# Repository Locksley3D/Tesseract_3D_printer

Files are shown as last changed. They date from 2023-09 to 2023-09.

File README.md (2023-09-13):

# Tesseract 3D printer

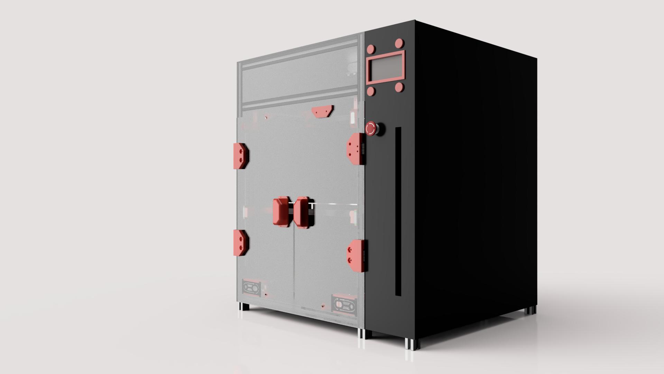
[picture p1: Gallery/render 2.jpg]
Side render of the Tesseract 3D printer


### This repository contains all the design files, scripts, and configs for the Tesseract, A big format tool-changing 3D printer

Some notes for anyone trying to replicate this project. Every STL is sorted in the STL directory and anything that doesn't fit in any categories is in the useful prints section. Also while there is a BOM there might be some small things missing like screws and such, Furthermore if you are using the BOM as a purchasing guide, you should always get more of the small stuff like screws because there are screws for stuff like the electronics mounts that are not in the BOM. If you do decide to build this printer I want to reiterate that this is a project and not a printer that will work right after building. I would be glad to answer any and all questions about thing printer which you can either leave here as an issue or as a comment on the YouTube videos that are linked below 

[Overview on YouTube](https://www.youtube.com/watch?v=-t1q_ze4PNQ)

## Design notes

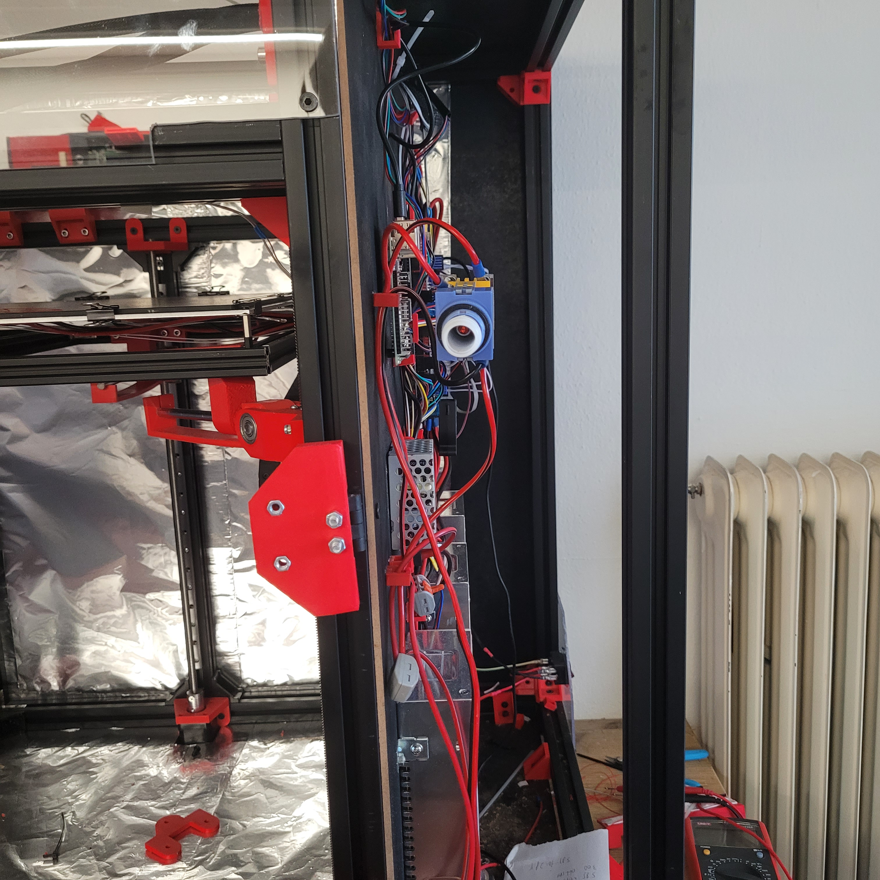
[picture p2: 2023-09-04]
Gallery/Electronics Side.jpg

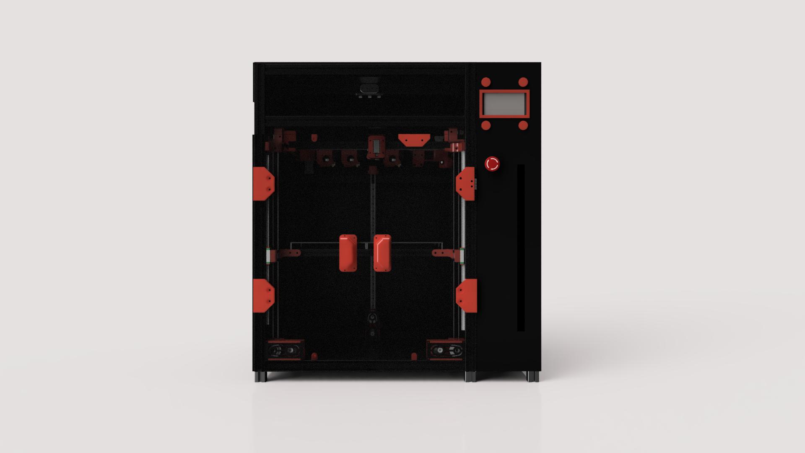
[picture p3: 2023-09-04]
Gallery/render 3.jpg

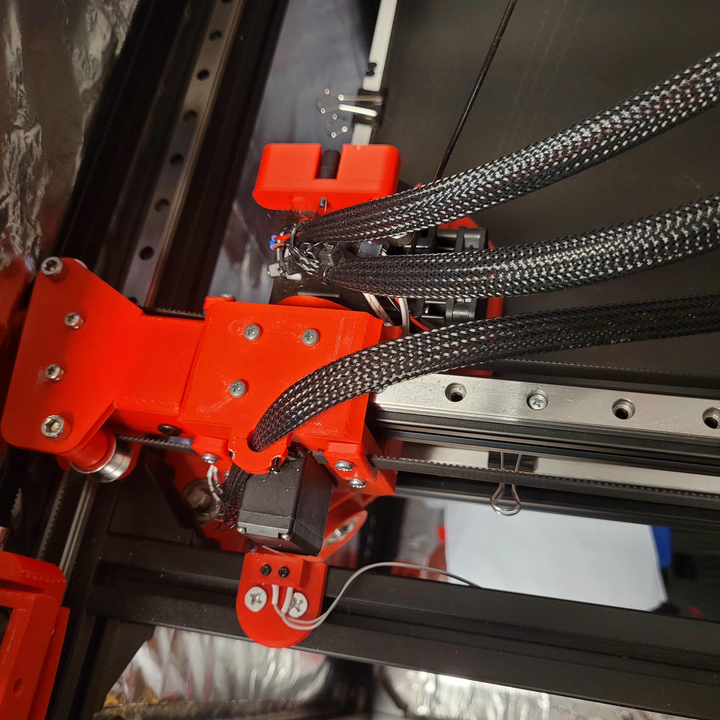
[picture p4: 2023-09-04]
Gallery/Toolhead mounted.jpg

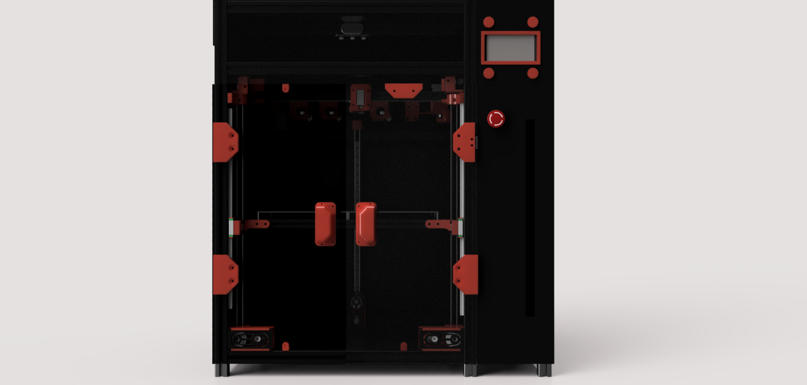
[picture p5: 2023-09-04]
Gallery/render 1.png

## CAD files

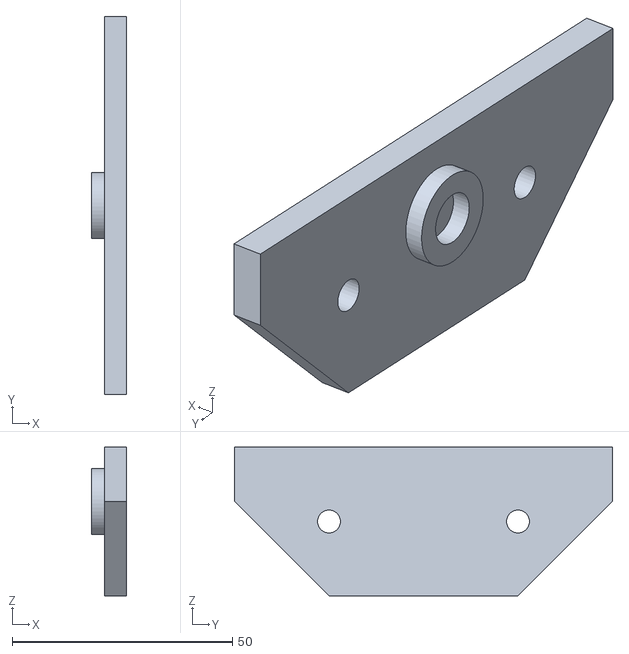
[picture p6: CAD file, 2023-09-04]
STLs/enclosure/door magnet mount.stl
8.00 x 85.9 x 33.8

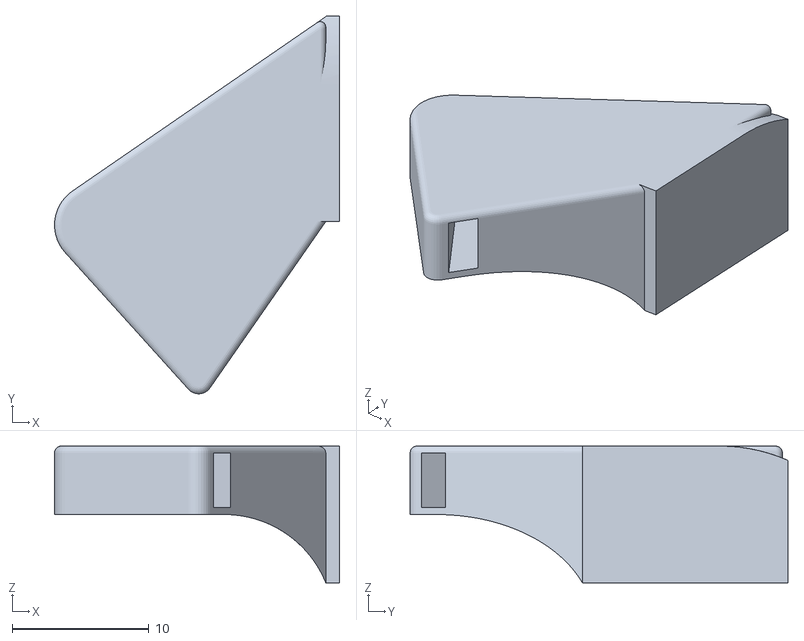
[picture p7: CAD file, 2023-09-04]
STLs/toolhead/toolhead zip tie mount.stl
20.8 x 27.6 x 10.0

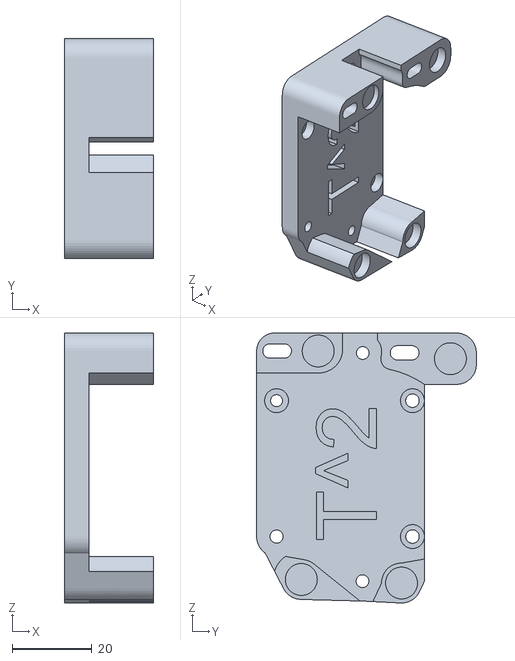
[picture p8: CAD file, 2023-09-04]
STLs/tools/hemera docking plate.stl
22.2 x 55.0 x 67.6

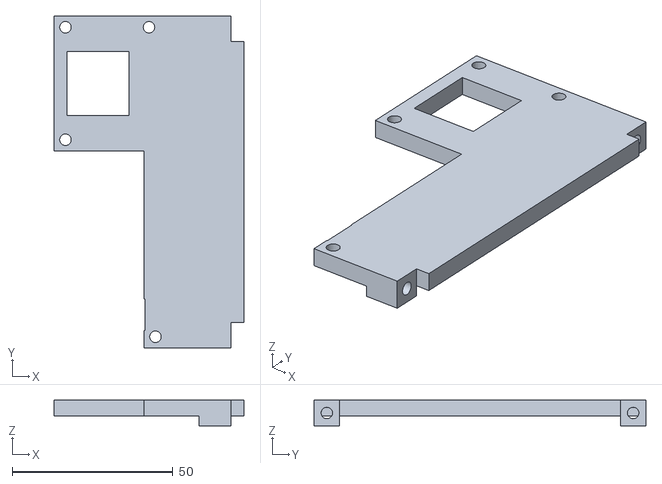
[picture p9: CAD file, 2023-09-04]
STLs/usefull prints/right transmission top plate.stl
59.0 x 103.3 x 8.00

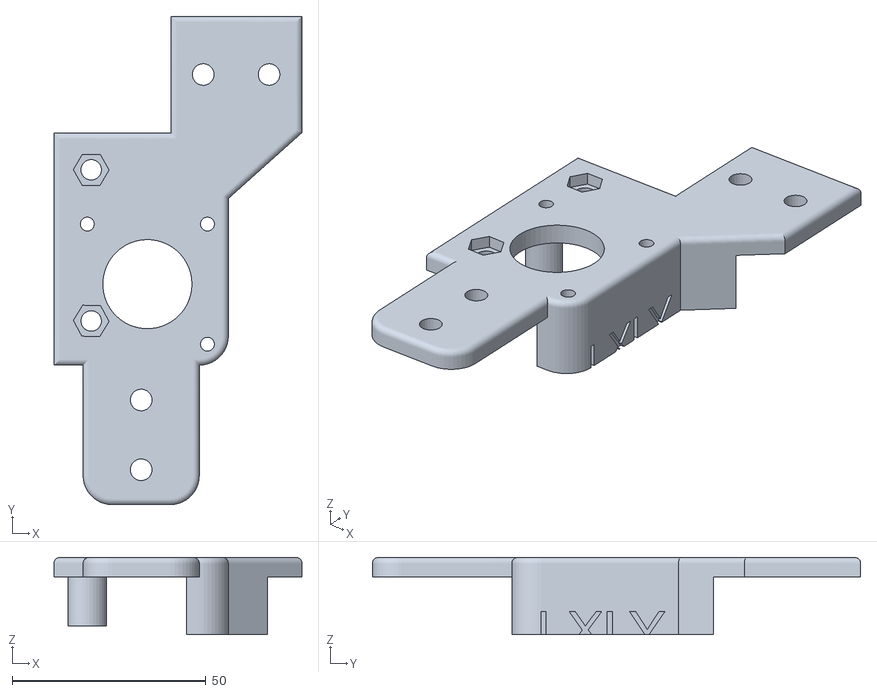
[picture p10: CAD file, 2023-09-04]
STLs/xy axis/right stepper mount to.stl
64.0 x 126.0 x 19.9

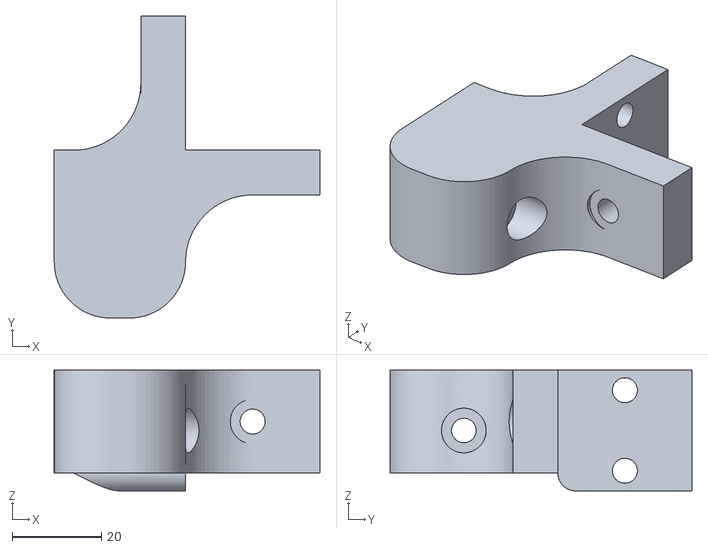
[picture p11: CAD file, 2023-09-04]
STLs/z axis/right belt idler mount.stl
59.3 x 67.5 x 27.0

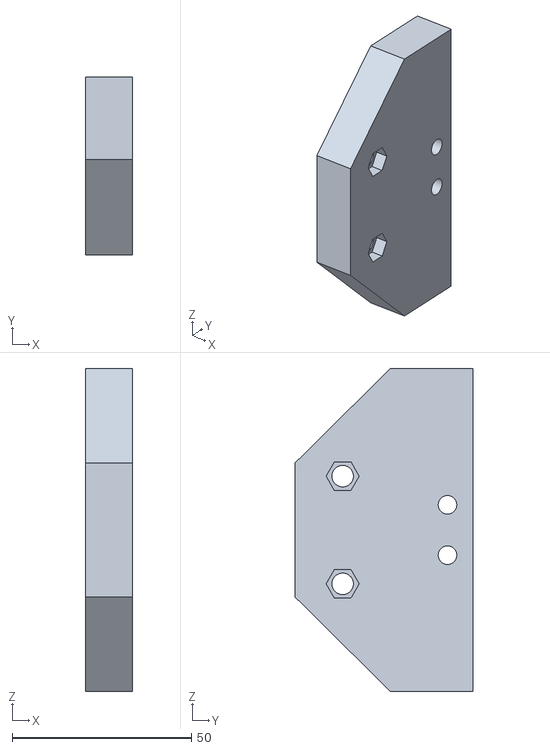
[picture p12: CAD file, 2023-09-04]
STLs/enclosure/right hinge.stl
13.0 x 49.6 x 90.0

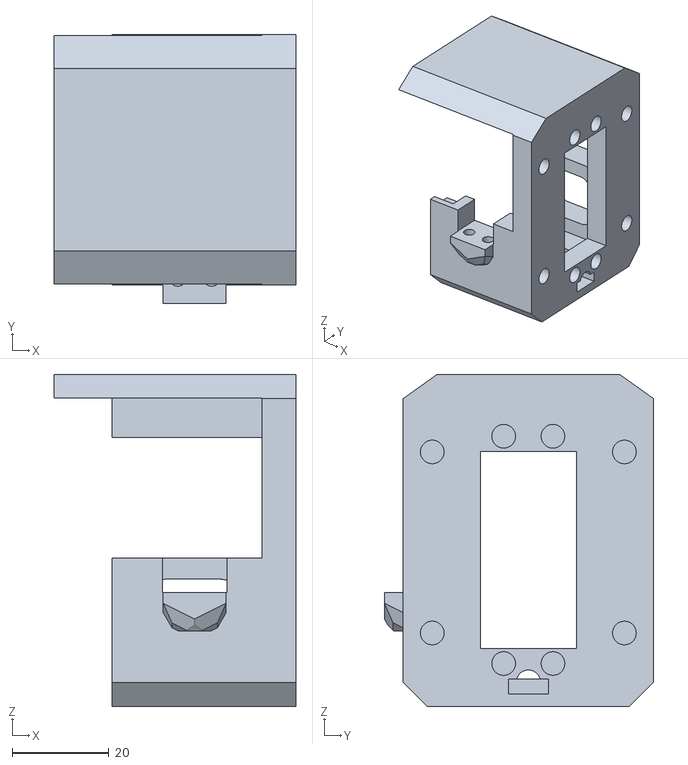
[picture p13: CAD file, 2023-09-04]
STLs/toolhead/toolhead servo mount.stl
49.9 x 55.5 x 68.5

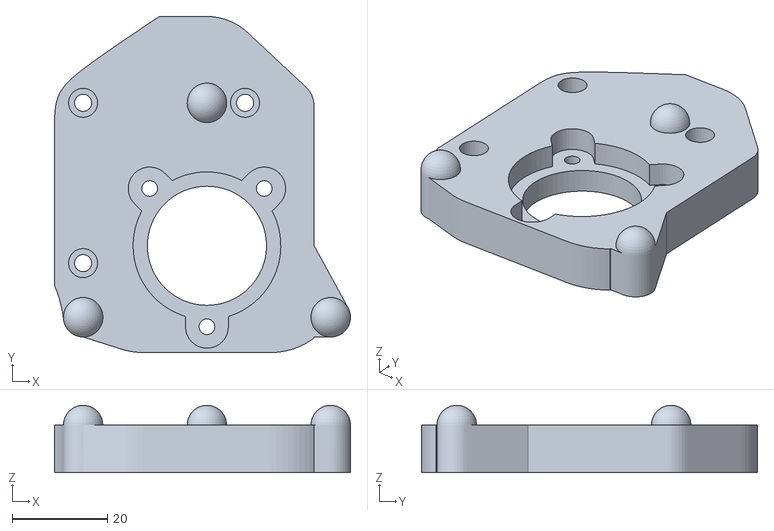
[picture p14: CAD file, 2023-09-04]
STLs/tools/hemera toolplate.stl
62.1 x 70.5 x 14.1

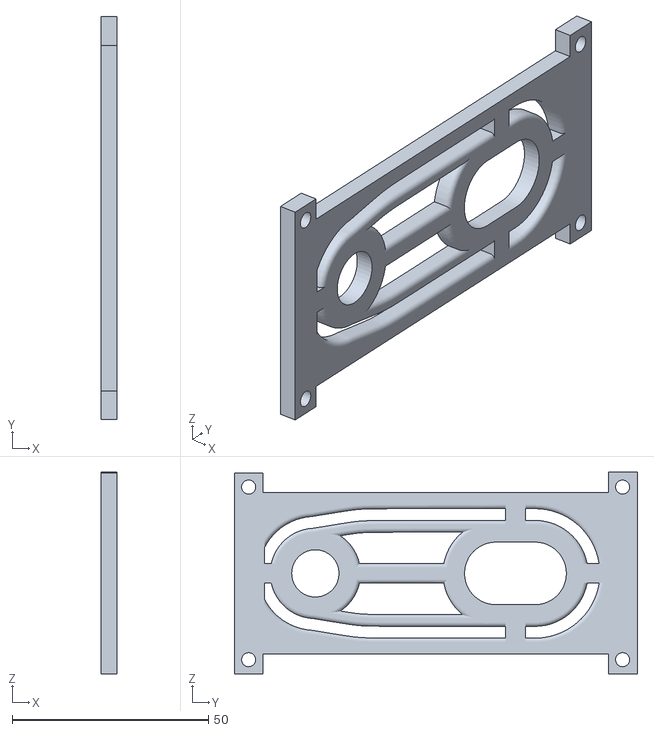
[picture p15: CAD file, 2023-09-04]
STLs/usefull prints/left transmission faceplate.stl
4.00 x 102.7 x 51.4

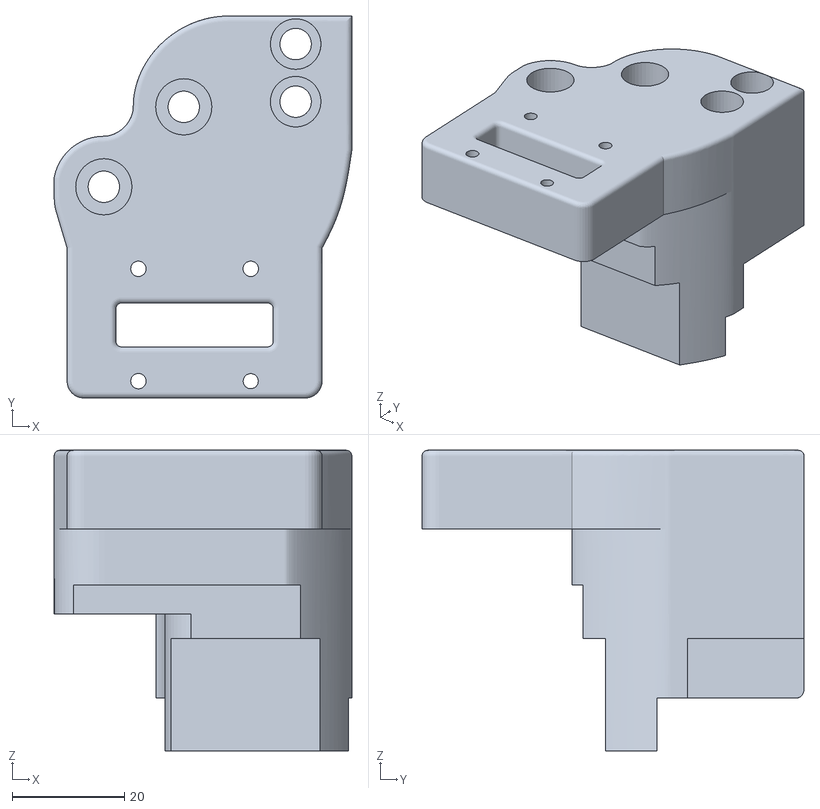
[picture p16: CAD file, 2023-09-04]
STLs/xy axis/left x gantry block.stl
53.0 x 68.0 x 53.5

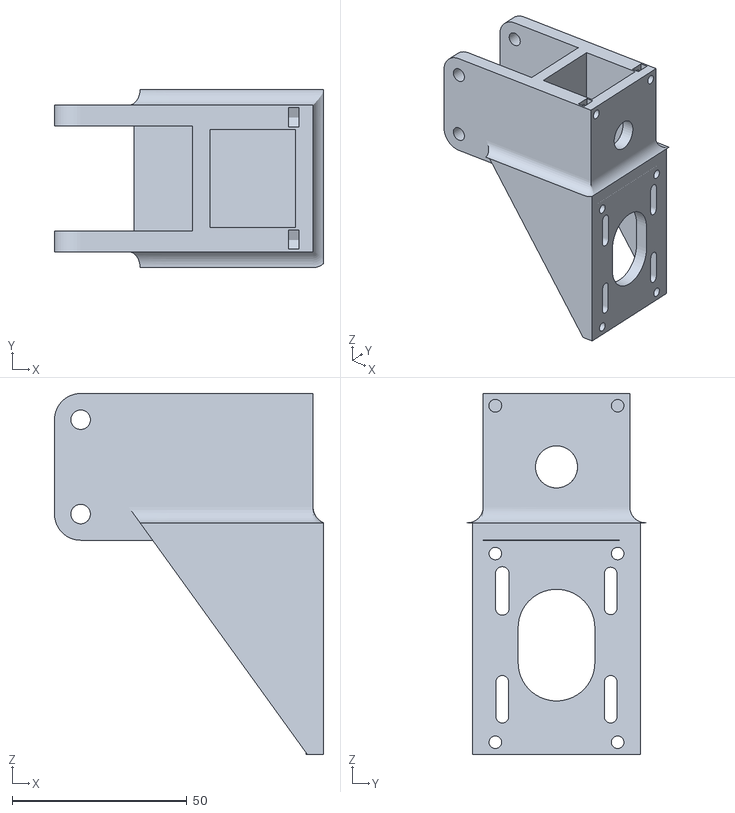
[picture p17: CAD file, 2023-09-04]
STLs/z axis/back transmission.stl
77.0 x 51.0 x 103.3

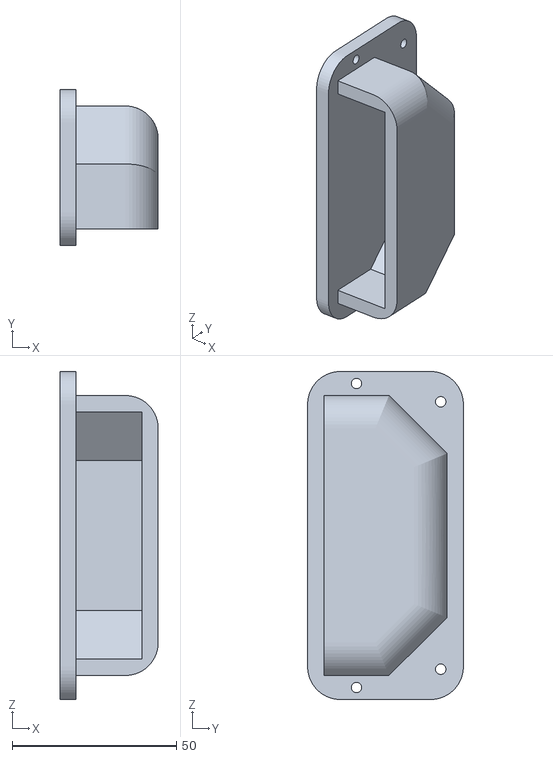
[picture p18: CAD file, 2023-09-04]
STLs/enclosure/left door handle.stl
30.0 x 47.5 x 100.0

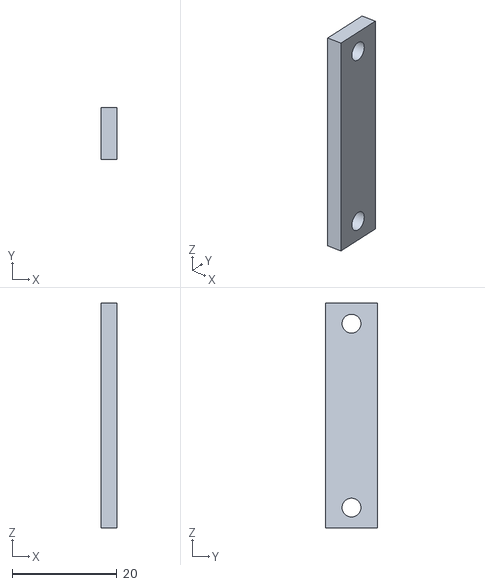
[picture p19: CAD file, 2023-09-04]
STLs/toolhead/toolhead belt lock.stl
3.00 x 10.0 x 43.0

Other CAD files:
STLs/tools/tool cradle.stl
STLs/usefull prints/zip tie mount.stl
STLs/xy axis/right tensioner.stl
STLs/z axis/z axis belt lock .stl
STLs/enclosure/door magnet holder.stl
STLs/enclosure/left hinge.stl
STLs/enclosure/right door handle.stl
STLs/enclosure/triangle cover with logo.stl
STLs/enclosure/triangle cover.stl
STLs/toolhead/maxwell kinematic coupler plate.stl
STLs/toolhead/toolhead servo cap.stl
STLs/usefull prints/camera cover.stl
STLs/usefull prints/camera mount.stl
STLs/usefull prints/left transmission top plate.stl
STLs/usefull prints/right transmission faceplate.stl
STLs/usefull prints/screen bezel.stl
STLs/xy axis/left belt tensioner .stl
STLs/xy axis/left stepper mount bottom.stl
STLs/xy axis/left stepper mount top.stl
STLs/xy axis/left tensioner idler mount.stl
STLs/xy axis/left x gantry block cap.stl
STLs/xy axis/right stepper mount bottom.stl
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

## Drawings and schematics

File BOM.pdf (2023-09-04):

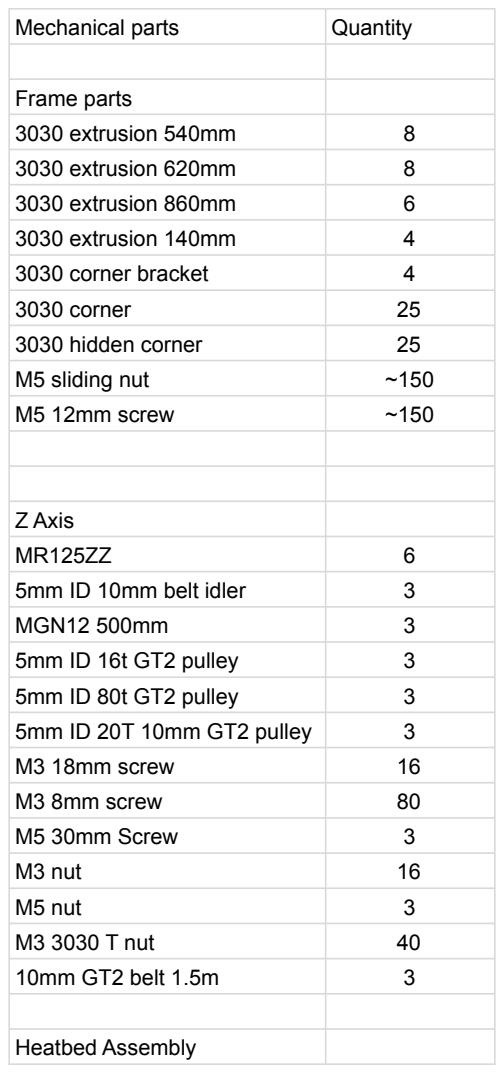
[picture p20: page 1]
Mechanical parts; Quantity; Frame parts; 3030 extrusion 540mm; 3030 extrusion 620mm; 3030 extrusion 860mm; 3030 extrusion 140mm; 3030 corner bracket; 3030 corner; 3030 hidden corner; M5 sliding nut; M5 12mm screw; Z Axis; 5mm ID 10mm belt idler; MGN12 500mm; 5mm ID 16t GT2 pulley; 5mm ID 80t GT2 pulley; 5mm ID 20T 10mm GT2 pulley; M3 18mm screw; M3 8mm screw; M5 30mm Screw; M3 nut; M5 nut; M3 3030 T nut; 10mm GT2 belt 1.5m; Heatbed Assembly

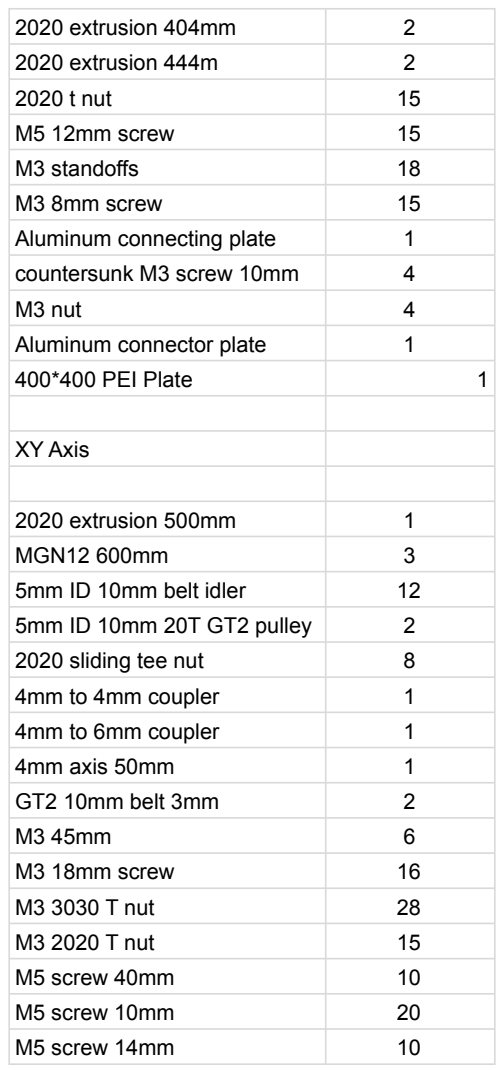
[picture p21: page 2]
2020 extrusion 404mm; 2020 extrusion 444m; 2020 t nut; M5 12mm screw; M3 standoffs; M3 8mm screw; Aluminum connecting plate; countersunk M3 screw 10mm; M3 nut; Aluminum connector plate; 400*400 PEI Plate; XY Axis; 2020 extrusion 500mm; MGN12 600mm; 5mm ID 10mm belt idler; 5mm ID 10mm 20T GT2 pulley; 2020 sliding tee nut; 4mm to 4mm coupler; 4mm to 6mm coupler; 4mm axis 50mm; GT2 10mm belt 3mm; M3 18mm screw; M3 3030 T nut; M3 2020 T nut; M5 screw 40mm; M5 screw 10mm; M5 screw 14mm

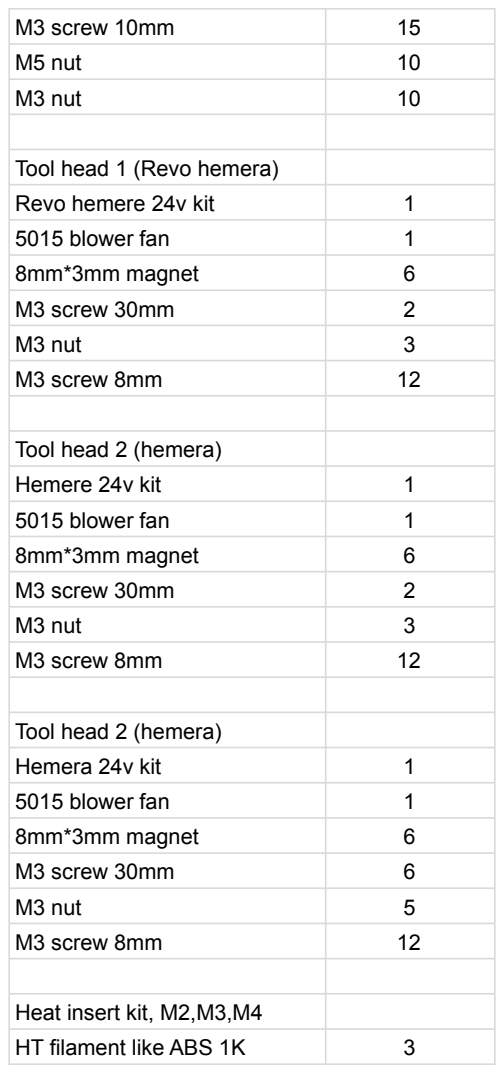
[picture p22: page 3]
M3 screw 10mm; M5 nut; M3 nut; Revo hemere 24v kit; 5015 blower fan; 8mm*3mm magnet; M3 screw 30mm; M3 screw 8mm; Hemere 24v kit; Hemera 24v kit; HT filament like ABS 1K

Tool head 1 (Revo hemera)

Tool head 2 (hemera)

Heat insert kit, M2,M3,M4

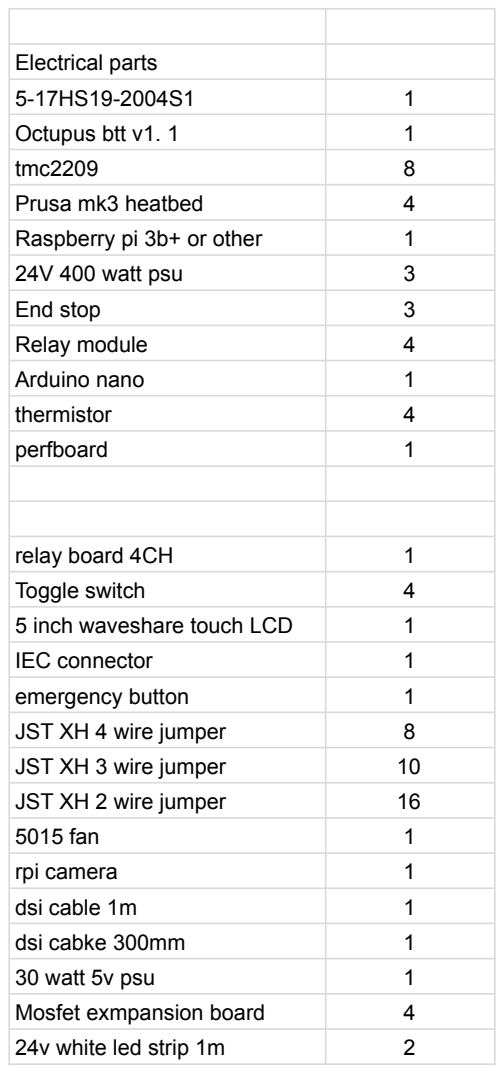
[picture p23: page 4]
Electrical parts; Octupus btt v1. 1; tmc2209; Prusa mk3 heatbed; Raspberry pi 3b+ or other; 24V 400 watt psu; End stop; Relay module; Arduino nano; thermistor; perfboard; relay board 4CH; Toggle switch; 5 inch waveshare touch LCD; IEC connector; emergency button; JST XH 4 wire jumper; JST XH 3 wire jumper; JST XH 2 wire jumper; 5015 fan; rpi camera; dsi cable 1m; dsi cabke 300mm; 30 watt 5v psu; Mosfet exmpansion board; 24v white led strip 1m

WS2812B 500mm | 1
Cabling of varying sizes | //

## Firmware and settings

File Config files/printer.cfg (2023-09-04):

[include mainsail.cfg]
[include MacrosAndPins.cfg]
[include tools.cfg]
[include led_progress.cfg]

 # This file contains common pin mappings for the BigTreeTech OctoPus V1.
# To use this config, the firmware should be compiled for the STM32F446 with a "32KiB bootloader"
# Enable "extra low-level configuration options" and select the "12MHz crystal" as clock reference

# after running "make", copy the generated "klipper/out/klipper.bin" file to a
# file named "firmware.bin" on an SD card and then restart the OctoPus with that SD card.

# See docs/Config_Reference.md for a description of parameters.

[stepper_x]
step_pin: PF13
dir_pin: PF12
enable_pin: !PF14
microsteps: 32
rotation_distance: 40
endstop_pin: !PG14
position_endstop:0
position_max:400
homing_speed: 200

[tmc2209 stepper_x]
uart_pin: PC4
run_current: 1.100
interpolate: false
sense_resistor: 0.110
stealthchop_threshold: 99999

[stepper_y]
step_pin: PG0
dir_pin: PG1
enable_pin: !PF15
microsteps: 32
rotation_distance: 40
endstop_pin: !PG13
position_endstop: 0
position_max: 470
homing_speed: 200

[tmc2209 stepper_y]
uart_pin: PD11
interpolate: false
run_current: 1.100
sense_resistor: 0.110
stealthchop_threshold: 99999

[stepper_z]
step_pin: PF11
dir_pin: !PG3
enable_pin: !PG5
microsteps: 16
rotation_distance: 40#46.7712
gear_ratio: 60:16
endstop_pin: probe:z_virtual_endstop  #!PG12
position_min:  -10
#position_endstop: -1.4  #1.25
position_max: 430
homing_speed: 10
second_homing_speed: 1
 
[tmc2209 stepper_z]
uart_pin: PC6
run_current: 0.900
sense_resistor: 0.110
#stealthchop_threshold: 999999

[stepper_z1]
step_pin: PG4
dir_pin: PC1
enable_pin: !PA0
microsteps: 16
rotation_distance: 40#46.7712
gear_ratio: 60:16

[tmc2209 stepper_z1]
uart_pin: PC7
run_current: 0.900
sense_resistor: 0.110
#stealthchop_threshold: 999999

[stepper_z2]
step_pin: PF9
dir_pin: !PF10
enable_pin: !PG2
microsteps: 16
rotation_distance: 40#46.7712
gear_ratio: 60:16

[tmc2209 stepper_z2]
uart_pin: PF2
run_current: 0.900
sense_resistor: 0.110
#stealthchop_threshold: 999999

[extruder]
step_pin: PC13
dir_pin: PF0
enable_pin: !PF1
heater_pin: PA2 # HE0
sensor_pin:  PF4
microsteps: 16
rotation_distance: 7.823960880195599
nozzle_diameter: 0.400
filament_diameter: 1.750
sensor_type: ATC Semitec 104GT-2
#control: pid
#pid_Kp: 22.2
#pid_Ki: 1.08
#pid_Kd: 114
min_temp: 0
max_temp: 285

[tmc2209 extruder]
uart_pin: PE4
run_current: 0.700
sense_resistor: 0.110
#stealthchop_threshold: 999999

[extruder1]
step_pin: PE2
dir_pin: PE3
enable_pin: !PD4
heater_pin: PA3 # HE0
sensor_pin:  PF6
microsteps: 16
rotation_distance: 7.823960880195599
nozzle_diameter: 0.400
filament_diameter: 1.750
sensor_type: ATC Semitec 104GT-2
control: pid
pid_Kp: 22.2
pid_Ki: 1.08
pid_Kd: 114
min_temp: 0
max_temp: 300


[tmc2209 extruder1]
uart_pin: PE1
run_current: 0.900
sense_resistor: 0.110
#stealthchop_threshold: 999999

[extruder2]
step_pin: PE6
dir_pin: PA14
enable_pin: !PE0
heater_pin: PB10 # HE0
sensor_pin:  PF5
microsteps: 16
rotation_distance: 7.823960880195599
nozzle_diameter: 0.400
filament_diameter: 1.750
sensor_type: ATC Semitec 104GT-2
control: pid
pid_Kp: 22.2
pid_Ki: 1.08
pid_Kd: 114
min_temp: 0
max_temp: 300


[tmc2209 extruder2]
uart_pin: PD3
run_current: 0.700
sense_resistor: 0.110
#stealthchop_threshold: 999999

#-----------------------------------------------------------------------------------------------

[probe]
z_offset: -4.753 #11.35
X_offset: -24.287
Y_offset: -39.616
pin: !PG15
# samples: 3
# sample_retract_dist: 2.0
# lift_speed: 5.0
# samples_result: median
# samples_tolerance: 0.100
# samples_tolerance_retries: 5


[z_tilt]
# z_positions: 170,391.9   #205,391.9
#              403,-42.25   #-14.7,-68(-40.4)
#              -49.7,-42.25  #428,-68(-40.4)
# points: 0 ,10
#         340,10
#         340,305
#         0,305
z_positions: 235,380
             498,-92
             -46,-92
points: 10,5
        370,5
        370,320
        10,320

speed:200
horizontal_move_z: 7
# retries:1
# retry_tolerance:0.2



[bed_mesh]
speed: 200
horizontal_move_z: 2
mesh_min: 10,10
mesh_max: 360,320
probe_count: 5,4


[safe_z_home]
home_xy_position:192,145
speed: 200
z_hop_speed: 10.0


#[extruder1]
#step_pin: PF9
#dir_pin: PF10
#enable_pin: !PG2
#heater_pin: PA3 # HE1
#sensor_pin: PF5
#...

#[extruder2]
#step_pin: PC13
#dir_pin: PF0
#enable_pin: !PF1
#heater_pin: PB10 # HE2
#sensor_pin: PF6
#...

#[extruder3]
#step_pin: PE2
#dir_pin: PE3
#enable_pin: !PD4
#heater_pin: PB11 # HE3
#sensor_pin: PF7
#...

#[extruder4]
#step_pin: PE6
#dir_pin: PA14
#enable_pin: !PE0
#...

[heater_bed]
heater_pin: PA1
sensor_pin: PF3
sensor_type: NTC 100K MGB18-104F39050L32
#control: pid
#pid_kp: 58.437
#pid_ki: 2.347
#pid_kd: 363.769
min_temp: 0
max_temp: 120

[fan_generic partcooling_1]
pin: PD14 

[fan_generic partcooling_2]
pin: PD13

[fan_generic partcooling_3]
pin: PD15

[heater_fan extruder]
pin: PE5 
heater: extruder

[heater_fan extruder1]
pin: PA8
heater: extruder1

[heater_fan extruder2]
pin: PD12
heater: extruder2

[neopixel bar]
pin:PB0
chain_count:13
color_order: GRB
initial_RED: 0.0
initial_GREEN: 1
initial_BLUE: 0.0
# initial_WHITE: 0.0
#   See the "led" section for information on these parameters.

# [fan]
# pin: PD14 # FAN0

# [heater_fan fan1]
# pin: PD14 # FAN1
# #heater_temp: 50.0

#[heater_fan fan2]
#pin: PD12 # FAN2

#[heater_fan fan3]
#pin: PD13 # FAN3

#[heater_fan fan4]
#pin: PD14 # FAN4

#[heater_fan fan5]
#pin: PD15 # FAN5

[temperature_sensor mcu_temp]
sensor_type: temperature_mcu

[mcu]
serial: /dev/serial/by-id/usb-Klipper_stm32f446xx_11002900085053424E363420-if00

[mcu rpi]
serial: /tmp/klipper_host_mcu

[mpu9250]
i2c_mcu: rpi
i2c_bus: i2c.1

[resonance_tester]
accel_chip: mpu9250
probe_points:
    185, 170, 20  # an example

#restart_method: command

# setup for PA9, PA10 USART1_tx / rx directly connected to the RPI GPIO TX / RX pins
# These are the pins the OctoPus uses for its built in RPI 40 pin connector
# only connect GND, TX, RX - supply 5v power to the RPI separately
# do not cross over TX/RX - it is done internally on the OctoPus PCB.
# Use "sudo raspi-config" to disable the serial terminal - but enable the serial port.
# When running "make menuconfig" you must un-select the USB Serial check box

# [input_shaper]
# shaper_freq_x: 39.2
# shaper_type_x: mzv
# shaper_freq_y: 27.8
# shaper_type_y: mzv


[printer]
kinematics: corexy
max_velocity: 300
max_accel: 3500
max_z_velocity: 12
max_z_accel: 50


########################################
# TMC2208 configuration
########################################

#[tmc2208 stepper_x]
#uart_pin: PC4
#run_current: 0.800
#hold_current: 0.500
#stealthchop_threshold: 999999

#[tmc2208 stepper_y]
#uart_pin: PD11
#run_current: 0.800
#hold_current: 0.500
#stealthchop_threshold: 999999

#[tmc2208 stepper_z]
#uart_pin: PC6
#run_current: 0.650
#hold_current: 0.450
#stealthchop_threshold: 999999

#[tmc2208 extruder]
#uart_pin: PC7
#run_current: 0.800
#hold_current: 0.500
#stealthchop_threshold: 999999

#[tmc2208 extruder1]
#uart_pin: PF2
#run_current: 0.800
#hold_current: 0.500
#stealthchop_threshold: 999999

#[tmc2208 extruder2]
#uart_pin: PE4
#run_current: 0.800
#hold_current: 0.500
#stealthchop_threshold: 999999

#[tmc2208 extruder3]
#uart_pin: PE1
#run_current: 0.8
#hold_current: 0.5
#stealthchop_threshold: 999999

#[tmc2208 extruder4]
#uart_pin: PD3
#run_current: 0.8
#hold_current: 0.5
#stealthchop_threshold: 999999


########################################
# TMC2130 configuration
########################################

#[tmc2130 stepper_x]
#cs_pin: PC4
#run_current: 0.800
#hold_current: 0.500
#stealthchop_threshold: 0
#spi_software_mosi_pin: PA7
#spi_software_miso_pin: PA6
#spi_software_sclk_pin: PA5

#[tmc2130 stepper_y]
#cs_pin: PD11
#run_current: 0.800
#hold_current: 0.500
#stealthchop_threshold: 0
#spi_software_mosi_pin: PA7
#spi_software_miso_pin: PA6
#spi_software_sclk_pin: PA5

#[tmc2130 stepper_z]
#cs_pin: PC6
#run_current: 0.800
#hold_current: 0.500
#stealthchop_threshold: 0
#spi_software_mosi_pin: PA7
#spi_software_miso_pin: PA6
#spi_software_sclk_pin: PA5

#[tmc2130 extruder]
#cs_pin: PC7
#run_current: 0.800
#hold_current: 0.500
#stealthchop_threshold: 0
#spi_software_mosi_pin: PA7
#spi_software_miso_pin: PA6
#spi_software_sclk_pin: PA5

#[tmc2130 extruder1]
#cs_pin: PF2
#run_current: 0.800
#hold_current: 0.500
#stealthchop_threshold: 0
#spi_software_mosi_pin: PA7
#spi_software_miso_pin: PA6
#spi_software_sclk_pin: PA5

#[tmc2130 extruder2]
#cs_pin: PE4
#run_current: 0.800
#hold_current: 0.500
#stealthchop_threshold: 0
#spi_software_mosi_pin: PA7
#spi_software_miso_pin: PA6
#spi_software_sclk_pin: PA5

#[tmc2130 extruder3]
#cs_pin: PE1
#run_current: 0.800
#hold_current: 0.500
#stealthchop_threshold: 0
#spi_software_mosi_pin: PA7
#spi_software_miso_pin: PA6
#spi_software_sclk_pin: PA5
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

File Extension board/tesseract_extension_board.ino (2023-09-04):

#include <Stepper.h>

int thermistorPin1 = A0;
int thermistorPin2 = A1;
int thermistorPin3 = A2;

int relay1=6;
int relay2=4;
int relay3=7;
int relay4=8;

int input1=10;
int input2=11;
int input3=12;

float Vo1; 
float Vo2; 
float Vo3; 

int stepperpin1=3;
int stepperpin2=5;
int stepperpin3=9;
int stepperpin4=13;

int act=0;
String receivedCommand;
int recieved_status = 0;
int commands[8];
int speed;
int distance;
char data[20];

const int stepsPerRevolution = 2048;  
int command=0;


Stepper myStepper(stepsPerRevolution, 3, 9, 5, 13);

void setup() {
  pinMode(thermistorPin1,INPUT);
  pinMode(thermistorPin2,INPUT);
  pinMode(thermistorPin3,INPUT);
  pinMode(input1,INPUT_PULLUP);
  pinMode(input2,INPUT_PULLUP);
  pinMode(input3,INPUT_PULLUP);
  pinMode(relay1,OUTPUT);
  pinMode(relay2,OUTPUT);
  pinMode(relay3,OUTPUT);
  pinMode(relay4,OUTPUT);
  pinMode(stepperpin1,OUTPUT);
  pinMode(stepperpin2,OUTPUT);
  pinMode(stepperpin3,OUTPUT);
  pinMode(stepperpin4,OUTPUT);
  Serial.begin(9600);
  delay(25);
  Serial.println("Ready");
}

void loop() {
   readSerialPort();
     
      if(recieved_status==1){
        if(act==1){
          delay(15);
          Serial.print("Moving at ");
          Serial.print(distance);
          Serial.print(" at a speed of ");
          Serial.print(speed);
          myStepper.setSpeed(speed);
          myStepper.step(distance);
          }
         if(act==2){
          delay(15);
          Serial.print("Moving at ");
          Serial.print(distance);
          Serial.print(" at a speed of ");
          Serial.print(speed);          myStepper.setSpeed(speed);
          myStepper.step(-distance);
          } 

         if(act==3){
          delay(15);
          Serial.print("Turning relay one on");
          if(speed==1){
            digitalWrite(relay1,HIGH);
            }else if(speed==0){
            digitalWrite(relay1,LOW);  
            }
          }
         
         if(act==4){
          delay(15);
          Serial.print("Turning relay two on");
          if(speed==1){
            digitalWrite(relay2,HIGH);
            }else if(speed==0){
            digitalWrite(relay2,LOW);  
            }
          }  

         if(act==5){
          delay(15);
          Serial.print("Turning relay three on");
          if(speed==1){
            digitalWrite(relay3,HIGH);
            }else if(speed==0){
            digitalWrite(relay3,LOW);  
            }
          } 

          
         if(act==6){
          delay(15);
          Serial.print("Turning relay four on");
          if(speed==1){
            digitalWrite(relay4,HIGH);
            }else if(speed==0){
            digitalWrite(relay4,LOW);  
            }
          }  
         if(act==7){
          delay(15);
          Serial.print("Turning all relays on");
          if(speed==1){
            digitalWrite(relay1,HIGH);
            digitalWrite(relay2,HIGH);
            digitalWrite(relay3,HIGH);
            digitalWrite(relay4,HIGH);

            }else if(speed==0){
            digitalWrite(relay1,LOW);  
            digitalWrite(relay2,LOW);  
            digitalWrite(relay3,LOW);  
            digitalWrite(relay4,LOW);  

            }
          }    
        
        delay(20); 
        Serial.println("Done");   
        stopMotor();
        act=-1;
        recieved_status = 0;
        Serial.flush();
        delay(20);
      }
/*
  if(digitalRead(input1)==LOW){
    digitalWrite(relay1,HIGH);
  }else{
  digitalWrite(relay1,LOW);
  }
  
  if(digitalRead(input2)==LOW){
    digitalWrite(relay2,HIGH);
   }else{
  digitalWrite(relay2,LOW);
   }
  if(digitalRead(input3)==LOW){
    digitalWrite(relay3,HIGH);
   }else{
  digitalWrite(relay3,LOW);
   }
*/

   if (millis() %1000 <500){
  
  
  Vo1 = analogRead(thermistorPin1);
  Vo2 = analogRead(thermistorPin2);
  Vo3 = analogRead(thermistorPin3);
  /*
  Serial.print("Temperature1 : ");
  Serial.print(thermistorCalculate(Vo1));
  Serial.print(" ");
  Serial.print("Temperature2 : ");
  Serial.print(thermistorCalculate(Vo2));
  Serial.print(" ");
  Serial.print("Temperature3 : ");
  Serial.print(thermistorCalculate(Vo3));
  Serial.println(" ");   
  */
}
}

float thermistorCalculate(float input){
  float R2, tKelvin, tCelsius;
  const float Beta     = 3974.0;
  const float roomTemp = 298.15;   // room temperature in Kelvin
  const float Ro = 10000.0; // Resistance of the thermistor at roomTemp
  const float R1 = 9710.0;  // Resistnce of the known resistor  
  R2 = R1 * (1023.0 / (float)input - 1.0); // Resistance of the Thermistor
  tKelvin = (Beta * roomTemp) /
            (Beta + (roomTemp * log(R2 / Ro)));
  tCelsius = tKelvin - 273.15;
  return tCelsius;
  }


void readSerialPort(){
    int i=0;
    int counter=0;
    int k=0;
    int command=0;
 
    
    if (Serial.available()) {
        for(int j=0; j<3; j++){
            commands[j]=-1;
        }
       
        delay(10);
        receivedCommand = "";
        while (Serial.available() > 0) {
            data[i] = (char)Serial.read();
            // mporei na einai megalo to mnm mexri to \n
            i++;   
            if (i>=20){
                break;
            } 
            delay(1);   
        }   
        recieved_status = 1;
        Serial.flush();
        delay(20);
        for(i=0; i<20; i++){
            if(data[i]=='/' || data[i]==','){
                switch(counter){
                    case 1:
                        command=data[i-counter]-'0';
                        commands[k]=command;
                        break;
                    case 2:
                        command=(data[i-counter]-'0')*10 + (data[i-counter+1]-'0');
                        commands[k]=command;
                        break;
                    case 3:
                        command=(data[i-counter]-'0')*100 + (data[i-counter+1]-'0')*10 + (data[i-counter+2]-'0');
                        commands[k]=command;
                        break;
                    case 4:
                        command=(data[i-counter]-'0')*1000 + (data[i-counter+1]-'0')*100 + (data[i-counter+2]-'0')*10 + (data[i-counter+3]-'0');
                        commands[k]=command;
                        break;    
                    case 5:
                        command=(data[i-counter]-'0')*10000+(data[i-counter+1]-'0')*1000 + (data[i-counter+2]-'0')*100 + (data[i-counter+3]-'0')*10 + (data[i-counter+4]-'0');
                        commands[k]=command;
                        break;  
                    }
                counter=0;
                command=0;
                k++;
            }
            else{
                counter++;      
            }
        }
     
        act = commands[0];
        speed = commands[1];
        distance = commands[2];

    } 
}

void stopMotor(){
  digitalWrite(3,LOW);
  digitalWrite(5,LOW);
  digitalWrite(9,LOW);
  digitalWrite(13,LOW);
  
  }  

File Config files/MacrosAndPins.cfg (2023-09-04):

[output_pin tool_grab]
pin: rpi:gpio23 

[output_pin tool_release]
pin: rpi:gpio27

[output_pin enable_heatbeds]
pin: rpi:gpio5

[gcode_macro tool_grab]
gcode:
  SET_PIN PIN=tool_grab VALUE=1
  G4 P4000
  SET_PIN PIN=tool_grab VALUE=0

[gcode_macro T0]
gcode:
  KTCC_T0

[gcode_macro T1]
gcode:
  KTCC_T1

[gcode_macro T2]
gcode:
  KTCC_T2

[gcode_macro T3]
gcode:
  KTCC_T3

[gcode_macro DROP_ALL_TOOLS]
gcode:
  KTCC_TOOL_DROPOFF_ALL

[gcode_macro Pre_Print_Calibration]
gcode:
  G28 X
  G28 Y
  KTCC_TOOL_DROPOFF_ALL
  G28 Z
  Z_TILT_ADJUST
  Z_TILT_ADJUST
  BED_MESH_CALIBRATE



[gcode_macro tool_release]
gcode:
  SET_PIN PIN=tool_release VALUE=1
  G4 P4000
  SET_PIN PIN=tool_release VALUE=0

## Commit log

2023-09-04 Added all the STL files
    [back bed mount.stl, back belt idler mount.stl, back transmission.stl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]
2023-09-04 added printer config files
    [MacrosAndPins.cfg, printer.cfg, tools.cfg]
2023-09-04 added BOM
2023-09-04 Updated the BOM
